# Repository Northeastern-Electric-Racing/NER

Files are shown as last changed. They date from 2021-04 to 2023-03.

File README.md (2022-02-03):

View this project on [CADLAB.io](https://cadlab.io/project/23137/master/files). 

# NER
This is the GitHub repo for all code and schematics created for Northeastern's Electric Racing club.

- Embedded Software: Contains all new embedded code for the Teensy microcontrollers
    - Use Platformio (VS Code plugin) for building and uploading software
        - To install, follow the directions on [this page](https://docs.platformio.org/en/latest//integration/ide/vscode.html)
        - This involves installing VS Code and setting up the Platformio extension
    - CAN libraries (must install in Platformio for each project): 
        - Teensy: [FlexCAN_T4](https://github.com/tonton81/FlexCAN_T4)
        - Arduino: [Seeed Studio CAN BUS Shield](https://github.com/Seeed-Studio/CAN_BUS_Shield)
- ArduinoCode: Old Arduino code for electrical subsystems, NOT UPDATED
    - Required CAN library: [Seeed Studio CAN BUS Shield](https://github.com/Seeed-Studio/CAN_BUS_Shield)
    - To install:
        1. Open the arduino IDE
        2. Go to Tools -> Manage Libraries...
        3. Search "CAN-BUS Shield" and install the associated library
- Schematics: Electrical schematics, created in KiCad, viewable online in CADlab.io or in the desktop client
- Project Manangement: This area has migrated to the [NER-PM-Dashboard repo](https://github.com/Northeastern-Electric-Racing/NER-PM-Dashboard)

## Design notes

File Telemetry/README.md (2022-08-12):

# Telemetry Python Scripts
Currently only the getCSV.py script is working, which converts the files in the logs directory to a csv file with the processed data. To use, run the following command:
- python getCSV.py -name="fileName.csv" -id=00 -data="Data Name" -n=0
- The flags in the command are optional, but do the following:
  - '-name="fileName.csv"' sets the output csv filename (default is output.txt)
  - '-id=00' sets an id to filter the data on, which must be in decimal (default is no filter to show all data)
  - '-data="Data Name"' sets a filter on the data from a specific id by the name in the description column (default is no filter to show all data from an id)
  - '-n=0' sets the format of the timestamp (0 for default string version or 1 for a numeric value)
- To graph a specific data value, filter by the correct -id and -data parameters and use a value of 1 for -n, then graphing the data vs timestamp columns in excel should be straightforward
The `drafts` directory contains unfinished scripts, with development moved to the Telemetry Hub

### Input/Output Directories
The scripts process all of the data in the /log_active directory and send an output to the /outputs directory. 
- Place old logs that we don't want to process but still want to keep in the /log_legacy directory

### TODO
- Add more behavior to graphing scripts
- Add full command line to control behavior through one main

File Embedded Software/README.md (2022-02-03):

# TODO
### All boards
- Add EEPROM support

### Dashboard
- Verify shutdown detect/precharge sequencing

### Pedal Box
- Brake pressure sensor updates

### TCU
- Add SD card logging
- Add accelerometer
- Add GPS
- Add Xbee transfers
- Calculations for vehicle speed
- Timestamp data

### Brake Light
- Add diff temp sensor

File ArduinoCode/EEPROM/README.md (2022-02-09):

# New Telemetry Test/Implementation Code

### Functionalities Achieved:

Writing and Reading to/from EEPROM <br />
Writing to SD Card <br />
Writing Sample Sensor Data to SD Card based on saved EEPROM Parameters <br />

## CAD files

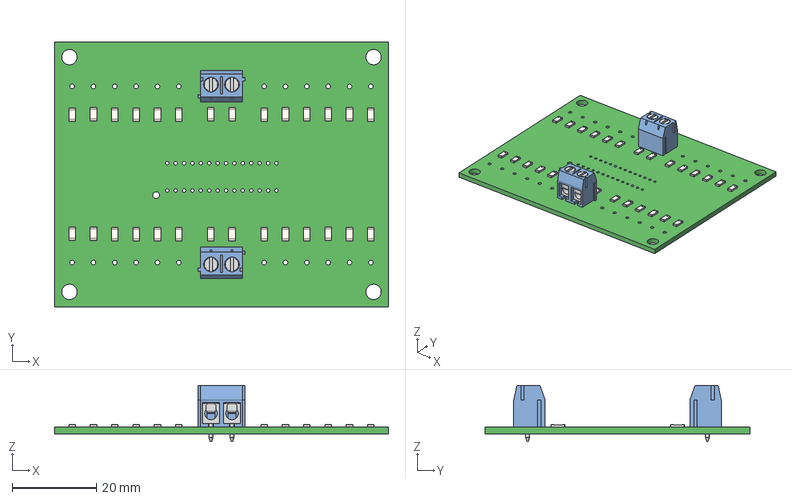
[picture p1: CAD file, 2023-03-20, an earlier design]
Schematics/Shutdown Summary/OLD (Deprecated)/Battery Managment/Therm_PCB/Therms.step
79.5 x 63.0 x 13.4 mm

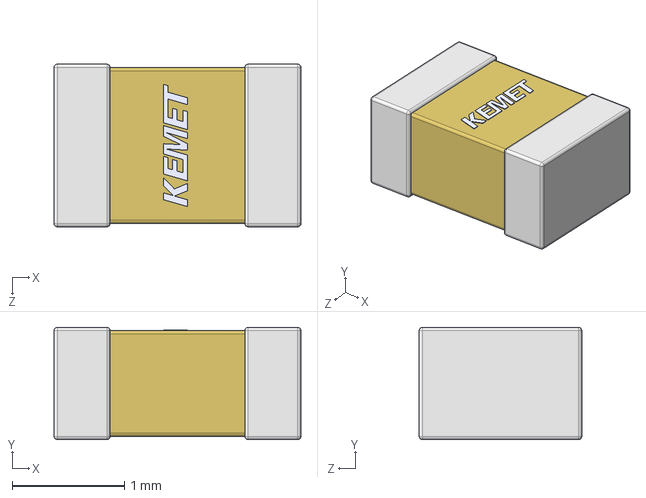
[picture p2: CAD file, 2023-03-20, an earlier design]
Schematics/Shutdown Summary/OLD (Deprecated)/TSAL/TSALpowerboard/3dmodel/C0805C105K9PACTU.STEP
2.20 x 1.00 x 1.45 mm

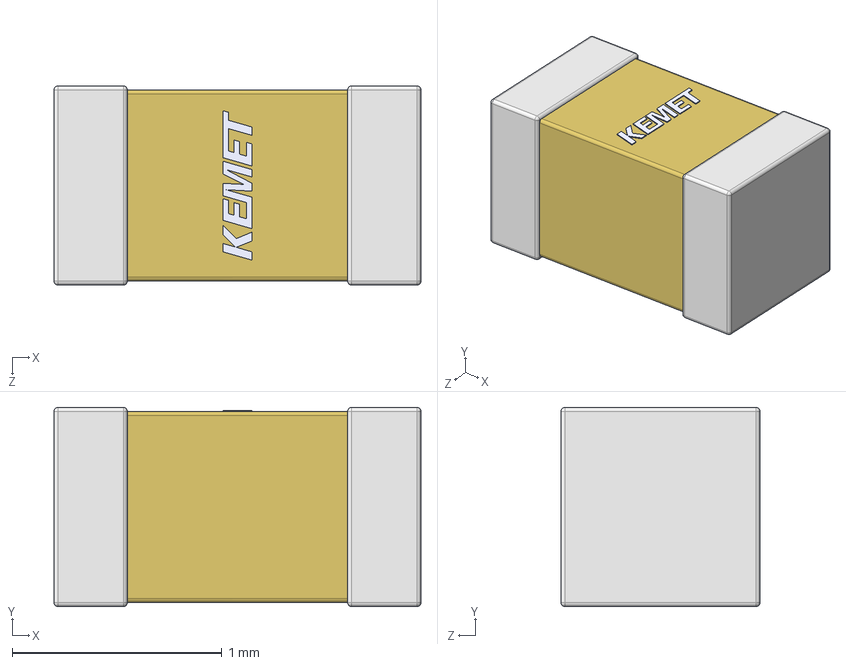
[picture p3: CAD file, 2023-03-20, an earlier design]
Schematics/Shutdown Summary/OLD (Deprecated)/TSAL/Tsalledboard/3dmodel/C0603C105K3RACTU.step
1.75 x 0.95 x 0.95 mm

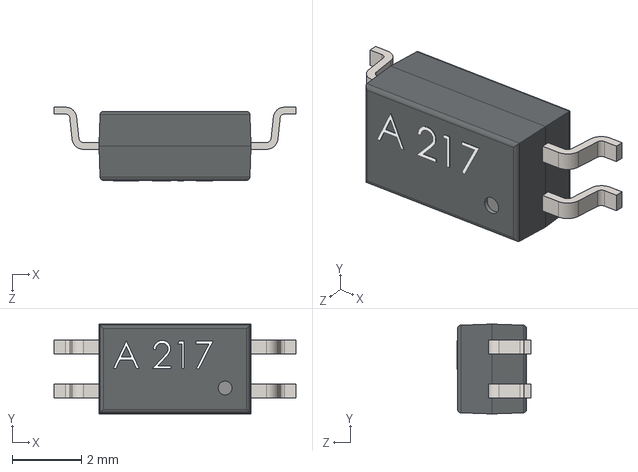
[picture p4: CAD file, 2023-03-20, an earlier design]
Schematics/Shutdown Summary/OLD (Deprecated)/TSAL/TSALpowerboard/3dmodel/User Library-ACPL-217-56DE.STEP
7.00 x 2.60 x 2.13 mm

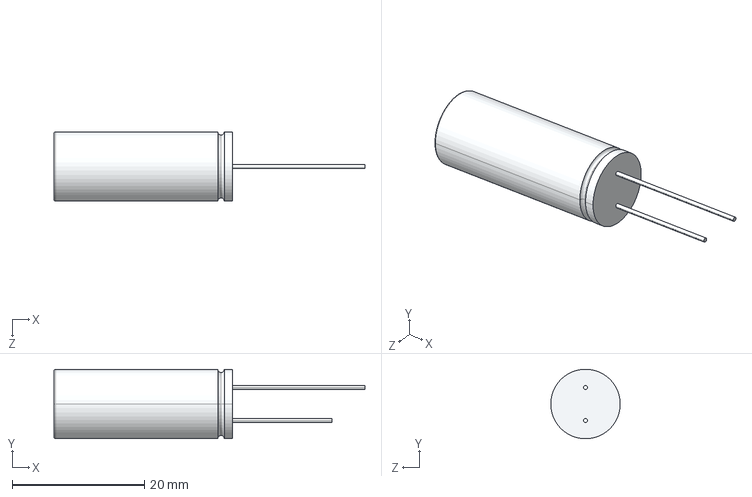
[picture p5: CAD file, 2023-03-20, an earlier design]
Schematics/Shutdown Summary/OLD (Deprecated)/TSAL/Tsalledboard/3dmodel/ESY827M025AH5AA.step
47.0 x 10.5 x 10.5 mm

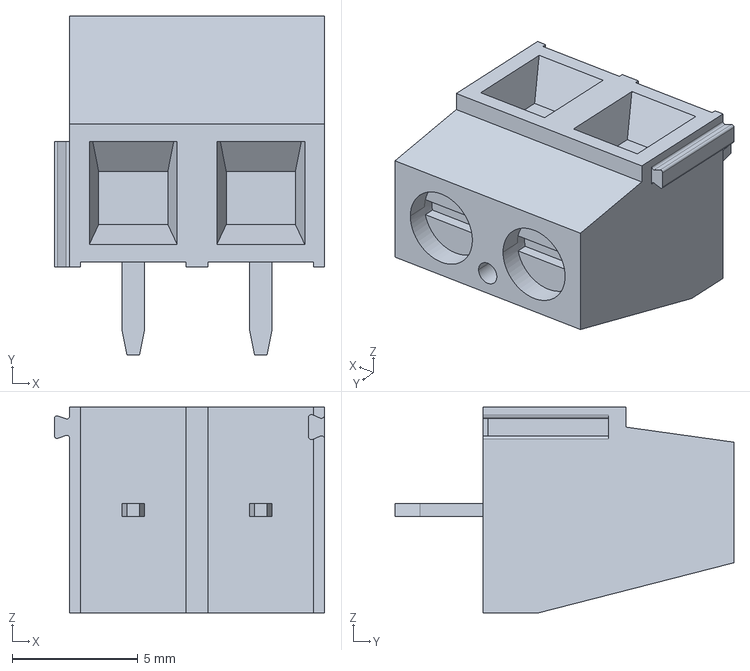
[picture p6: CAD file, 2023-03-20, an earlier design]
Schematics/Shutdown Summary/OLD (Deprecated)/TSAL/TSALpowerboard/3dmodel/c-282837-2-g2-3d.stp
10.8 x 13.5 x 8.20 mm

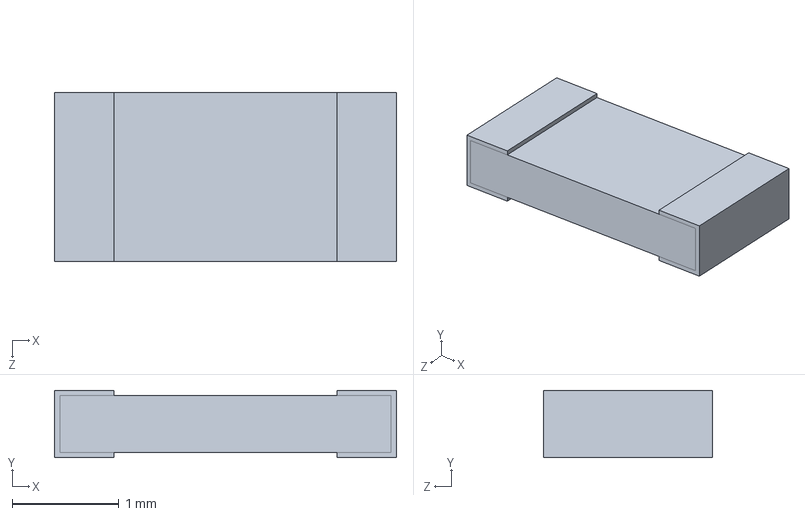
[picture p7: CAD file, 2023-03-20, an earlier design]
Schematics/Shutdown Summary/OLD (Deprecated)/Battery Managment/VoltTap_PCB/C1T5_CAD_Model.SLDPRT
3.20 x 0.63 x 1.58 mm

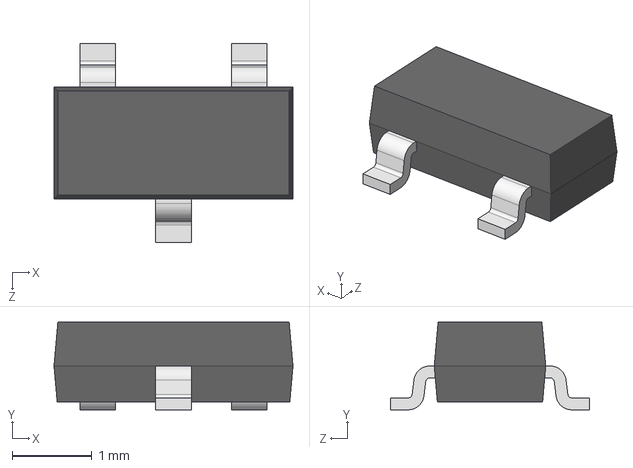
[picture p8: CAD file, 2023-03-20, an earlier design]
Schematics/Shutdown Summary/OLD (Deprecated)/TSAL/Tsalledboard/3dmodel/CircuitWorks-SOT-23.STEP
3.00 x 1.10 x 2.50 mm

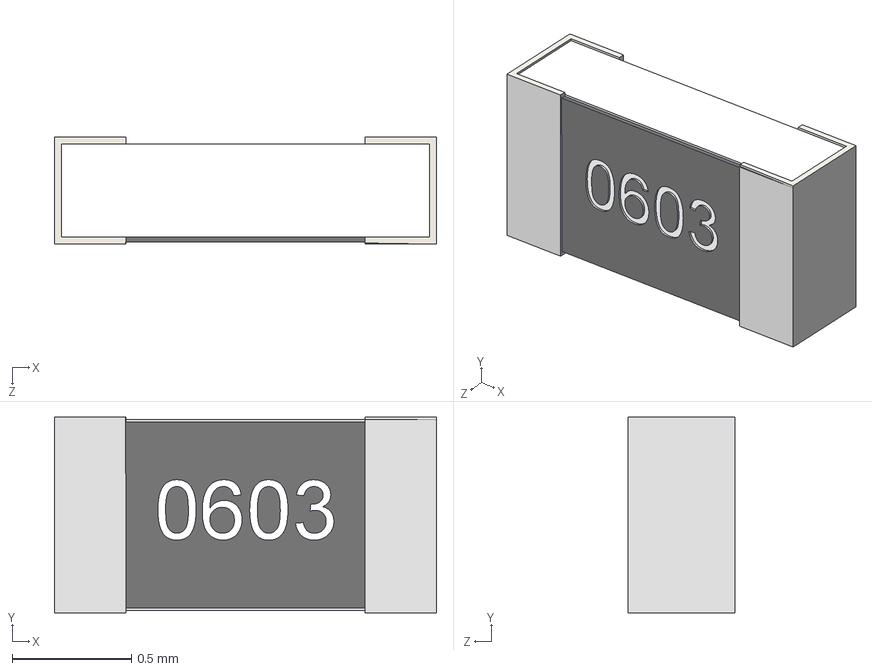
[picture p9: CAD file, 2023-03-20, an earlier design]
Schematics/Shutdown Summary/OLD (Deprecated)/TSAL/TSALpowerboard/3dmodel/Library-Panasonic0603.STEP
1.60 x 0.82 x 0.45 mm

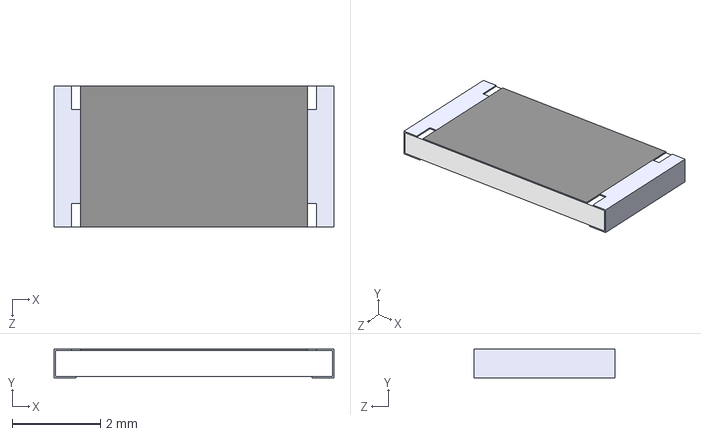
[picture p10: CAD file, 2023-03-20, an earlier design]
Schematics/Shutdown Summary/OLD (Deprecated)/TSAL/Tsalledboard/3dmodel/CRGP2512F560K--3DModel-STEP-46669.STEP
6.35 x 0.65 x 3.20 mm

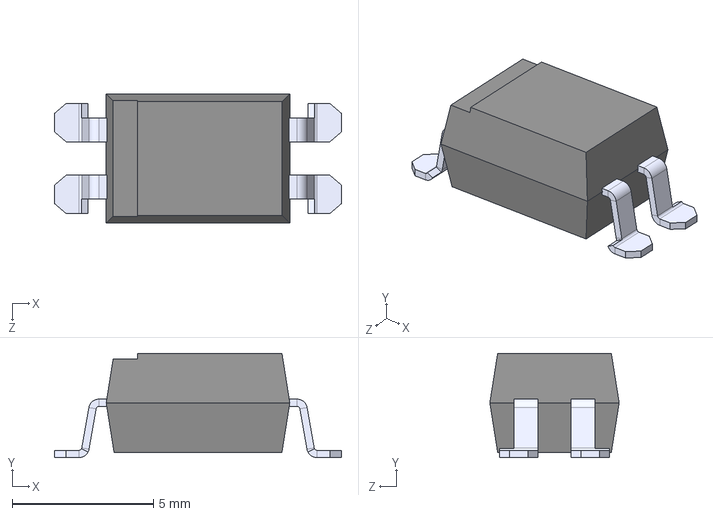
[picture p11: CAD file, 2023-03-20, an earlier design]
Schematics/Shutdown Summary/OLD (Deprecated)/TSAL/TSALpowerboard/3dmodel/SFH617A.STEP
10.2 x 3.69 x 4.58 mm

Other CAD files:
Schematics/Shutdown Summary/OLD (Deprecated)/Battery Managment/VoltTap_PCB/Board.step.SLDASM
Schematics/Shutdown Summary/OLD (Deprecated)/Battery Managment/VoltTap_PCB/C1T5_CAD_Model-0.step.SLDPRT
Schematics/Shutdown Summary/OLD (Deprecated)/Battery Managment/VoltTap_PCB/6120xx22021_LEVIER_COURT.step.SLDPRT
Schematics/Shutdown Summary/OLD (Deprecated)/Battery Managment/VoltTap_PCB/26.step.SLDPRT
Schematics/Shutdown Summary/OLD (Deprecated)/Battery Managment/Therm_PCB/Therms.SLDPRT
Schematics/Shutdown Summary/OLD (Deprecated)/Battery Managment/VoltTap_PCB/6120xx21621_PIN.step.SLDPRT
Schematics/Shutdown Summary/OLD (Deprecated)/Battery Managment/VoltTap_PCB/6911027100xx_CAGE.step.SLDPRT
Schematics/Shutdown Summary/OLD (Deprecated)/Battery Managment/VoltTap_PCB/6911027100xx_PIN.step.SLDPRT
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

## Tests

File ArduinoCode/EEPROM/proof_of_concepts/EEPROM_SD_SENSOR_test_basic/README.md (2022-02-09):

# Second EEPROM Test
### Integrating EEPROM Reading and Writing with SD Card Reading and Writing, Ultrasonic Distance Sensor Sample

Writes sensor parameters to the EEPROM (in this case, 10) to turn on the LED if the distance detected is
less than the specified parameters.
The distance and any important messages are written to the SD card in the DATA.txt file included

## Functionalities:

Writing to SD Card <br />
Reading and Writing to/from EEPROM <br />
Incorporating Sample Sensor (Ultrasonic Distance Sensor) <br />

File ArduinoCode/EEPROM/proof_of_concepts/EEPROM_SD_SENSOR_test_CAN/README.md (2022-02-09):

# Third EEPROM Test
### Using EEPROM Reading and Writing with SD Card Reading and Writing, Ultrasonic Distance Sensor Sample w/ CAN Bus Integration

Has configurable LED output pin and distance sensor parameter based on CAN configuration message. Turns on set LED pin if the ultrasonic distance sensor detects an object within the set parameters.
The distance data and any alerts are written to DATA.txt on an SD card

## TODO

Test Functionality on board <br />

<br />

## Functionalities:

Writing to SD Card <br /> <br />
Reading and Writing to/from EEPROM <br />
Pulling Pin #'s and Parameters from EEPROM <br /> <br />
Reconfiguring Pin #'s and Parameters based on CAN configuration message <br />
Sending configuration message <br /> <br />
Incorporating Sample Sensor (Ultrasonic Distance Sensor) <br />

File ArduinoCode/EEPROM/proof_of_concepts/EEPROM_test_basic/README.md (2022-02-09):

# Initial EEPROM test
###### Writes Data to EEPROM and Reads it

Demonstrates writing to the EEPROM and reading the values by accessing different addresses
Screenshot included is sample reading from the EEPROM

## Functionalities:

Writing and Reading to/from EEPROM

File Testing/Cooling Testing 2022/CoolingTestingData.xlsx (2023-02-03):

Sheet: Fans Only
3.9654 | 4.0475 | 3.7511 | 3.8927 | 3.7594 | 3.9576 | 3.9849 | 3.9842 | 3.9228 | 3.8056 | 4.0448 | 4.0424 | 4.0391 | 4.0897 | 4.0242 | 4.0383 | 4.0366 | 3.7822
Pack Voltage | 71.17
Max Voltage | 4.09
Min Voltage | 3.75
Cell Delta | 0.34
Temperature
25 | 25 | 24 | 25 | 24 | 25 | 25 | 24 | 24 | 24 | 25 | 25 | 25 | 25 | 25 | 25 | 25 | 26 | 25 | 25 | 25 | 25
Voltage
3.9654 | 4.0475 | 3.7511 | 3.8928 | 3.7595 | 3.9575 | 3.9849 | 3.9841 | 3.9228 | 3.8065 | 4.0447 | 4.0424 | 4.0391 | 4.0898 | 4.0245 | 4.0384 | 4.0363 | 3.7833
Pack Voltage | 71.17
Max Voltage | 4.09
Min Voltage | 3.75
Cell Delta | 0.34
Temperature
25 | 25 | 24 | 25 | 24 | 25 | 25 | 24 | 24 | 24 | 25 | 25 | 25 | 25 | 25 | 25 | 25 | 26 | 25 | 25 | 25 | 25
Voltage
3.826 | 3.9046 | 3.6572 | 3.7705 | 3.6667 | 3.8679 | 3.8842 | 3.8924 | 3.7997 | 3.7151 | 3.9267 | 3.9386 | 3.9272 | 3.9833 | 3.9304 | 3.9452 | 3.9395 | 3.6926
Pack Voltage | 69.27
Max Voltage | 3.98
Min Voltage | 3.66
Cell Delta | 0.33
Temperature
25 | 25 | 24 | 25 | 24 | 25 | 25 | 24 | 24 | 24 | 25 | 25 | 25 | 25 | 25 | 25 | 25 | 26 | 25 | 25 | 25 | 25
Voltage
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

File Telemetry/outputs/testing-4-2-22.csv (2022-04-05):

time | message_id | description | value
2021-01-01T00:00:01.633Z | 171 | POST Fault Lo | 0000000000000000
2021-01-01T00:00:01.633Z | 171 | POST Fault Hi | 0000000000000000
2021-01-01T00:00:01.633Z | 171 | Run Fault Lo | 0000100000000000
2021-01-01T00:00:01.633Z | 171 | Run Fault Hi | 0000000000000000
2021-01-01T00:00:03.638Z | 171 | POST Fault Lo | 0000000000000000
2021-01-01T00:00:03.638Z | 171 | POST Fault Hi | 0000000000000000
2021-01-01T00:00:03.638Z | 171 | Run Fault Lo | 0000100000000000
2021-01-01T00:00:03.638Z | 171 | Run Fault Hi | 0000000000000000
2021-01-01T00:00:06.141Z | 171 | POST Fault Lo | 0000000000000000
2021-01-01T00:00:06.141Z | 171 | POST Fault Hi | 0000000000000000
2021-01-01T00:00:06.141Z | 171 | Run Fault Lo | 0000100000000000
2021-01-01T00:00:06.141Z | 171 | Run Fault Hi | 0000000000000000
2021-01-01T00:00:07.690Z | 171 | POST Fault Lo | 0000000000000000
2021-01-01T00:00:07.690Z | 171 | POST Fault Hi | 0000000000000000
2021-01-01T00:00:07.690Z | 171 | Run Fault Lo | 0000100000000000
2021-01-01T00:00:07.690Z | 171 | Run Fault Hi | 0000000000000000
2021-01-01T00:00:09.639Z | 171 | POST Fault Lo | 0000000000000000
2021-01-01T00:00:09.639Z | 171 | POST Fault Hi | 0000000000000000
2021-01-01T00:00:09.639Z | 171 | Run Fault Lo | 0000100000000000
2021-01-01T00:00:09.639Z | 171 | Run Fault Hi | 0000000000000000
2021-01-01T00:00:11.638Z | 171 | POST Fault Lo | 0000000000000000
2021-01-01T00:00:11.638Z | 171 | POST Fault Hi | 0000000000000000
2021-01-01T00:00:11.638Z | 171 | Run Fault Lo | 0000100000000000
2021-01-01T00:00:11.638Z | 171 | Run Fault Hi | 0000000000000000
2021-01-01T00:00:13.790Z | 171 | POST Fault Lo | 0000000000000000
2021-01-01T00:00:13.790Z | 171 | POST Fault Hi | 0000000000000000
2021-01-01T00:00:13.790Z | 171 | Run Fault Lo | 0000100000000000
2021-01-01T00:00:13.790Z | 171 | Run Fault Hi | 0000000000000000
2021-01-01T00:00:15.647Z | 171 | POST Fault Lo | 0000000000000000
2021-01-01T00:00:15.647Z | 171 | POST Fault Hi | 0000000000000000
2021-01-01T00:00:15.647Z | 171 | Run Fault Lo | 0000100000000000
2021-01-01T00:00:15.647Z | 171 | Run Fault Hi | 0000000000000000
2021-01-01T00:00:17.647Z | 171 | POST Fault Lo | 0000000000000000
2021-01-01T00:00:17.647Z | 171 | POST Fault Hi | 0000000000000000
2021-01-01T00:00:17.647Z | 171 | Run Fault Lo | 0000100000000000
2021-01-01T00:00:17.647Z | 171 | Run Fault Hi | 0000000000000000
2021-01-01T00:00:19.897Z | 171 | POST Fault Lo | 0000000000000000
2021-01-01T00:00:19.897Z | 171 | POST Fault Hi | 0000000000000000
2021-01-01T00:00:19.897Z | 171 | Run Fault Lo | 0000100000000000
2021-01-01T00:00:19.897Z | 171 | Run Fault Hi | 0000000000000000
2021-01-01T00:00:21.644Z | 171 | POST Fault Lo | 0000000000000000
2021-01-01T00:00:21.644Z | 171 | POST Fault Hi | 0000000000000000
2021-01-01T00:00:21.644Z | 171 | Run Fault Lo | 0000100000000000
2021-01-01T00:00:21.644Z | 171 | Run Fault Hi | 0000000000000000
2021-01-01T00:00:23.655Z | 171 | POST Fault Lo | 0000000000000000
2021-01-01T00:00:23.655Z | 171 | POST Fault Hi | 0000000000000000
2021-01-01T00:00:23.655Z | 171 | Run Fault Lo | 0000100000000000
2021-01-01T00:00:23.655Z | 171 | Run Fault Hi | 0000000000000000
2021-01-01T00:00:25.971Z | 171 | POST Fault Lo | 0000000000000000
2021-01-01T00:00:25.971Z | 171 | POST Fault Hi | 0000000000000000
2021-01-01T00:00:25.971Z | 171 | Run Fault Lo | 0000100000000000
2021-01-01T00:00:25.971Z | 171 | Run Fault Hi | 0000000000000000
2021-01-01T00:00:27.656Z | 171 | POST Fault Lo | 0000000000000000
2021-01-01T00:00:27.656Z | 171 | POST Fault Hi | 0000000000000000
2021-01-01T00:00:27.656Z | 171 | Run Fault Lo | 0000100000000000
2021-01-01T00:00:27.656Z | 171 | Run Fault Hi | 0000000000000000
2021-01-01T00:00:29.647Z | 171 | POST Fault Lo | 0000000000000000
2021-01-01T00:00:29.647Z | 171 | POST Fault Hi | 0000000000000000
2021-01-01T00:00:29.647Z | 171 | Run Fault Lo | 0000100000000000
2021-01-01T00:00:29.647Z | 171 | Run Fault Hi | 0000000000000000
2021-01-01T00:00:32.027Z | 171 | POST Fault Lo | 0000000000000000
2021-01-01T00:00:32.027Z | 171 | POST Fault Hi | 0000000000000000
2021-01-01T00:00:32.027Z | 171 | Run Fault Lo | 0000100000000000
2021-01-01T00:00:32.027Z | 171 | Run Fault Hi | 0000000000000000
2021-01-01T00:00:33.649Z | 171 | POST Fault Lo | 0000000000000000
2021-01-01T00:00:33.649Z | 171 | POST Fault Hi | 0000000000000000
2021-01-01T00:00:33.649Z | 171 | Run Fault Lo | 0000100000000000
2021-01-01T00:00:33.649Z | 171 | Run Fault Hi | 0000000000000000
2021-01-01T00:00:35.663Z | 171 | POST Fault Lo | 0000000000000000
2021-01-01T00:00:35.663Z | 171 | POST Fault Hi | 0000000000000000
2021-01-01T00:00:35.663Z | 171 | Run Fault Lo | 0000100000000000
2021-01-01T00:00:35.663Z | 171 | Run Fault Hi | 0000000000000000
2021-01-01T00:00:38.072Z | 171 | POST Fault Lo | 0000000000000000
2021-01-01T00:00:38.072Z | 171 | POST Fault Hi | 0000000000000000
2021-01-01T00:00:38.072Z | 171 | Run Fault Lo | 0000100000000000
2021-01-01T00:00:38.072Z | 171 | Run Fault Hi | 0000000000000000
2021-01-01T00:00:39.663Z | 171 | POST Fault Lo | 0000000000000000
2021-01-01T00:00:39.663Z | 171 | POST Fault Hi | 0000000000000000
2021-01-01T00:00:39.663Z | 171 | Run Fault Lo | 0000100000000000
2021-01-01T00:00:39.663Z | 171 | Run Fault Hi | 0000000000000000
2021-01-01T00:00:41.658Z | 171 | POST Fault Lo | 0000000000000000
2021-01-01T00:00:41.658Z | 171 | POST Fault Hi | 0000000000000000
2021-01-01T00:00:41.658Z | 171 | Run Fault Lo | 0000100000000000
2021-01-01T00:00:41.658Z | 171 | Run Fault Hi | 0000000000000000
2021-01-01T00:00:44.119Z | 171 | POST Fault Lo | 0000000000000000
2021-01-01T00:00:44.119Z | 171 | POST Fault Hi | 0000000000000000
2021-01-01T00:00:44.119Z | 171 | Run Fault Lo | 0000100000000000
2021-01-01T00:00:44.119Z | 171 | Run Fault Hi | 0000000000000000
2021-01-01T00:00:45.655Z | 171 | POST Fault Lo | 0000000000000000
2021-01-01T00:00:45.655Z | 171 | POST Fault Hi | 0000000000000000
2021-01-01T00:00:45.655Z | 171 | Run Fault Lo | 0000100000000000
2021-01-01T00:00:45.655Z | 171 | Run Fault Hi | 0000000000000000
2021-01-01T00:00:47.659Z | 171 | POST Fault Lo | 0000000000000000
2021-01-01T00:00:47.659Z | 171 | POST Fault Hi | 0000000000000000
2021-01-01T00:00:47.659Z | 171 | Run Fault Lo | 0000100000000000
2021-01-01T00:00:47.659Z | 171 | Run Fault Hi | 0000000000000000
2021-01-01T00:00:50.147Z | 171 | POST Fault Lo | 0000000000000000
2021-01-01T00:00:50.147Z | 171 | POST Fault Hi | 0000000000000000
2021-01-01T00:00:50.147Z | 171 | Run Fault Lo | 0000100000000000
2021-01-01T00:00:50.147Z | 171 | Run Fault Hi | 0000000000000000
2021-01-01T00:00:51.662Z | 171 | POST Fault Lo | 0000000000000000
2021-01-01T00:00:51.662Z | 171 | POST Fault Hi | 0000000000000000
2021-01-01T00:00:51.662Z | 171 | Run Fault Lo | 0000100000000000
2021-01-01T00:00:51.662Z | 171 | Run Fault Hi | 0000000000000000
2021-01-01T00:00:53.659Z | 171 | POST Fault Lo | 0000000000000000
2021-01-01T00:00:53.659Z | 171 | POST Fault Hi | 0000000000000000
2021-01-01T00:00:53.659Z | 171 | Run Fault Lo | 0000100000000000
2021-01-01T00:00:53.659Z | 171 | Run Fault Hi | 0000000000000000
2021-01-01T00:00:57.671Z | 171 | POST Fault Lo | 0000000000000000
2021-01-01T00:00:57.671Z | 171 | POST Fault Hi | 0000000000000000
2021-01-01T00:00:57.671Z | 171 | Run Fault Lo | 0000100000000000
2021-01-01T00:00:57.671Z | 171 | Run Fault Hi | 0000000000000000
2021-01-01T00:00:59.662Z | 171 | POST Fault Lo | 0000000000000000
2021-01-01T00:00:59.662Z | 171 | POST Fault Hi | 0000000000000000
2021-01-01T00:00:59.662Z | 171 | Run Fault Lo | 0000100000000000
2021-01-01T00:00:59.662Z | 171 | Run Fault Hi | 0000000000000000
2021-01-01T00:01:03.664Z | 171 | POST Fault Lo | 0000000000000000
2021-01-01T00:01:03.664Z | 171 | POST Fault Hi | 0000000000000000
2021-01-01T00:01:03.664Z | 171 | Run Fault Lo | 0000100000000000
2021-01-01T00:01:03.664Z | 171 | Run Fault Hi | 0000000000000000
2021-01-01T00:01:05.671Z | 171 | POST Fault Lo | 0000000000000000
2021-01-01T00:01:05.671Z | 171 | POST Fault Hi | 0000000000000000
2021-01-01T00:01:05.671Z | 171 | Run Fault Lo | 0000100000000000
2021-01-01T00:01:05.671Z | 171 | Run Fault Hi | 0000000000000000
2021-01-01T00:01:07.666Z | 171 | POST Fault Lo | 0000000000000000
2021-01-01T00:01:07.666Z | 171 | POST Fault Hi | 0000000000000000
2021-01-01T00:01:07.666Z | 171 | Run Fault Lo | 0000100000000000
2021-01-01T00:01:07.666Z | 171 | Run Fault Hi | 0000000000000000
2021-01-01T00:01:10.317Z | 171 | POST Fault Lo | 0000000000000000
2021-01-01T00:01:10.317Z | 171 | POST Fault Hi | 0000000000000000
2021-01-01T00:01:10.317Z | 171 | Run Fault Lo | 0000100000000000
2021-01-01T00:01:10.317Z | 171 | Run Fault Hi | 0000000000000000
2021-01-01T00:01:11.668Z | 171 | POST Fault Lo | 0000000000000000
2021-01-01T00:01:11.668Z | 171 | POST Fault Hi | 0000000000000000
2021-01-01T00:01:11.668Z | 171 | Run Fault Lo | 0000100000000000
2021-01-01T00:01:11.668Z | 171 | Run Fault Hi | 0000000000000000
2021-01-01T00:01:13.669Z | 171 | POST Fault Lo | 0000000000000000
2021-01-01T00:01:13.669Z | 171 | POST Fault Hi | 0000000000000000
2021-01-01T00:01:13.669Z | 171 | Run Fault Lo | 0000100000000000
2021-01-01T00:01:13.669Z | 171 | Run Fault Hi | 0000000000000000
2021-01-01T00:01:15.679Z | 171 | POST Fault Lo | 0000000000000000
2021-01-01T00:01:15.679Z | 171 | POST Fault Hi | 0000000000000000
2021-01-01T00:01:15.679Z | 171 | Run Fault Lo | 0000100000000000
2021-01-01T00:01:15.679Z | 171 | Run Fault Hi | 0000000000000000
2021-01-01T00:01:18.221Z | 171 | POST Fault Lo | 0000000000000000
2021-01-01T00:01:18.221Z | 171 | POST Fault Hi | 0000000000000000
2021-01-01T00:01:18.221Z | 171 | Run Fault Lo | 0000100000000000
2021-01-01T00:01:18.221Z | 171 | Run Fault Hi | 0000000000000000
2021-01-01T00:01:19.681Z | 171 | POST Fault Lo | 0000000000000000
2021-01-01T00:01:19.681Z | 171 | POST Fault Hi | 0000000000000000
2021-01-01T00:01:19.681Z | 171 | Run Fault Lo | 0000100000000000
2021-01-01T00:01:19.681Z | 171 | Run Fault Hi | 0000000000000000
2021-01-01T00:01:21.681Z | 171 | POST Fault Lo | 0000000000000000
2021-01-01T00:01:21.681Z | 171 | POST Fault Hi | 0000000000000000
2021-01-01T00:01:21.681Z | 171 | Run Fault Lo | 0000100000000000
2021-01-01T00:01:21.681Z | 171 | Run Fault Hi | 0000000000000000
2021-01-01T00:01:23.673Z | 171 | POST Fault Lo | 0000000000000000
2021-01-01T00:01:23.673Z | 171 | POST Fault Hi | 0000000000000000
2021-01-01T00:01:23.673Z | 171 | Run Fault Lo | 0000100000000000
2021-01-01T00:01:23.673Z | 171 | Run Fault Hi | 0000000000000000
2021-01-01T00:01:25.912Z | 171 | POST Fault Lo | 0000000000000000
2021-01-01T00:01:25.912Z | 171 | POST Fault Hi | 0000000000000000
2021-01-01T00:01:25.912Z | 171 | Run Fault Lo | 0000100000000000
2021-01-01T00:01:25.912Z | 171 | Run Fault Hi | 0000000000000000
2021-01-01T00:01:27.681Z | 171 | POST Fault Lo | 0000000000000000
2021-01-01T00:01:27.681Z | 171 | POST Fault Hi | 0000000000000000
2021-01-01T00:01:27.681Z | 171 | Run Fault Lo | 0000100000000000
2021-01-01T00:01:27.681Z | 171 | Run Fault Hi | 0000000000000000
2021-01-01T00:01:29.682Z | 171 | POST Fault Lo | 0000000000000000
2021-01-01T00:01:29.682Z | 171 | POST Fault Hi | 0000000000000000
2021-01-01T00:01:29.682Z | 171 | Run Fault Lo | 0000100000000000
2021-01-01T00:01:29.682Z | 171 | Run Fault Hi | 0000000000000000
2021-01-01T00:01:33.686Z | 171 | POST Fault Lo | 0000000000000000
2021-01-01T00:01:33.686Z | 171 | POST Fault Hi | 0000000000000000
2021-01-01T00:01:33.686Z | 171 | Run Fault Lo | 0000100000000000
2021-01-01T00:01:33.686Z | 171 | Run Fault Hi | 0000000000000000
2021-01-01T00:01:35.687Z | 171 | POST Fault Lo | 0000000000000000
2021-01-01T00:01:35.687Z | 171 | POST Fault Hi | 0000000000000000
2021-01-01T00:01:35.687Z | 171 | Run Fault Lo | 0000100000000000
2021-01-01T00:01:35.687Z | 171 | Run Fault Hi | 0000000000000000
2021-01-01T00:01:39.743Z | 171 | POST Fault Lo | 0000000000000000
2021-01-01T00:01:39.743Z | 171 | POST Fault Hi | 0000000000000000
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

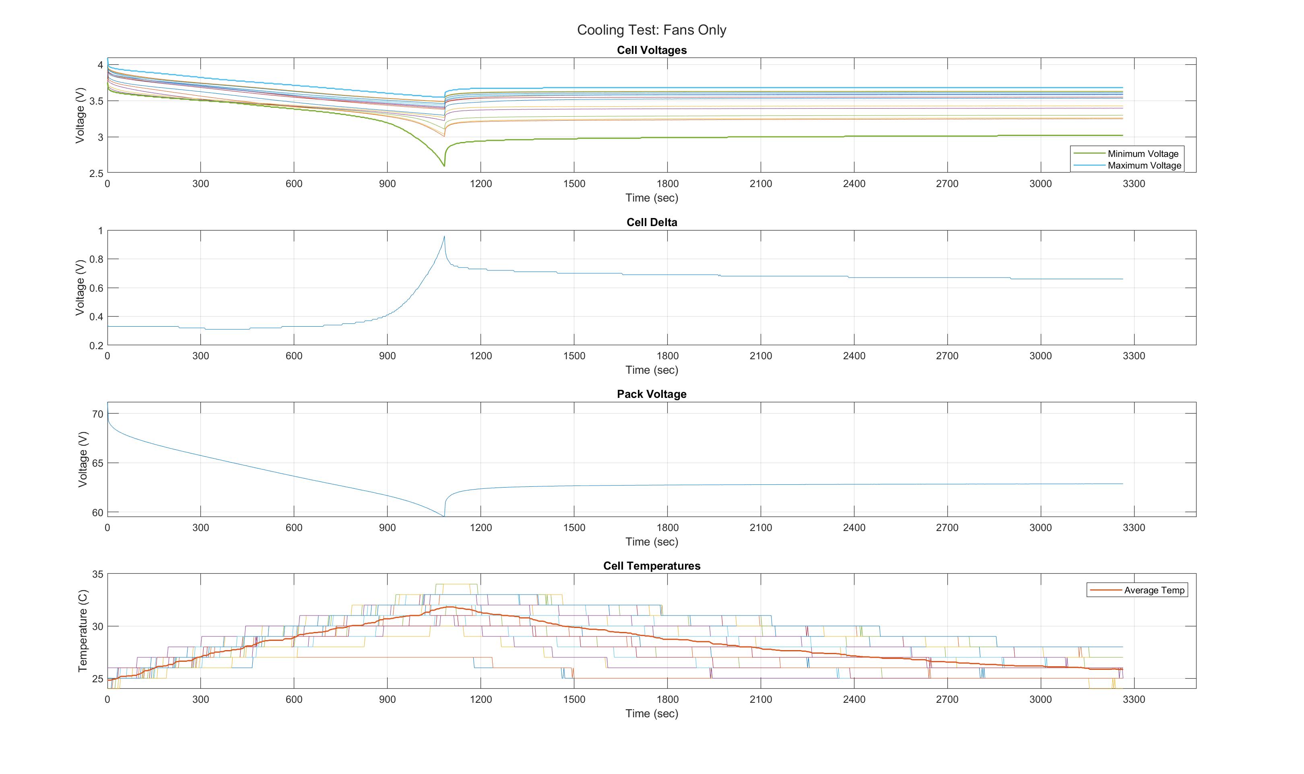
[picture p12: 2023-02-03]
Testing/Cooling Testing 2022/Fans Only.jpg

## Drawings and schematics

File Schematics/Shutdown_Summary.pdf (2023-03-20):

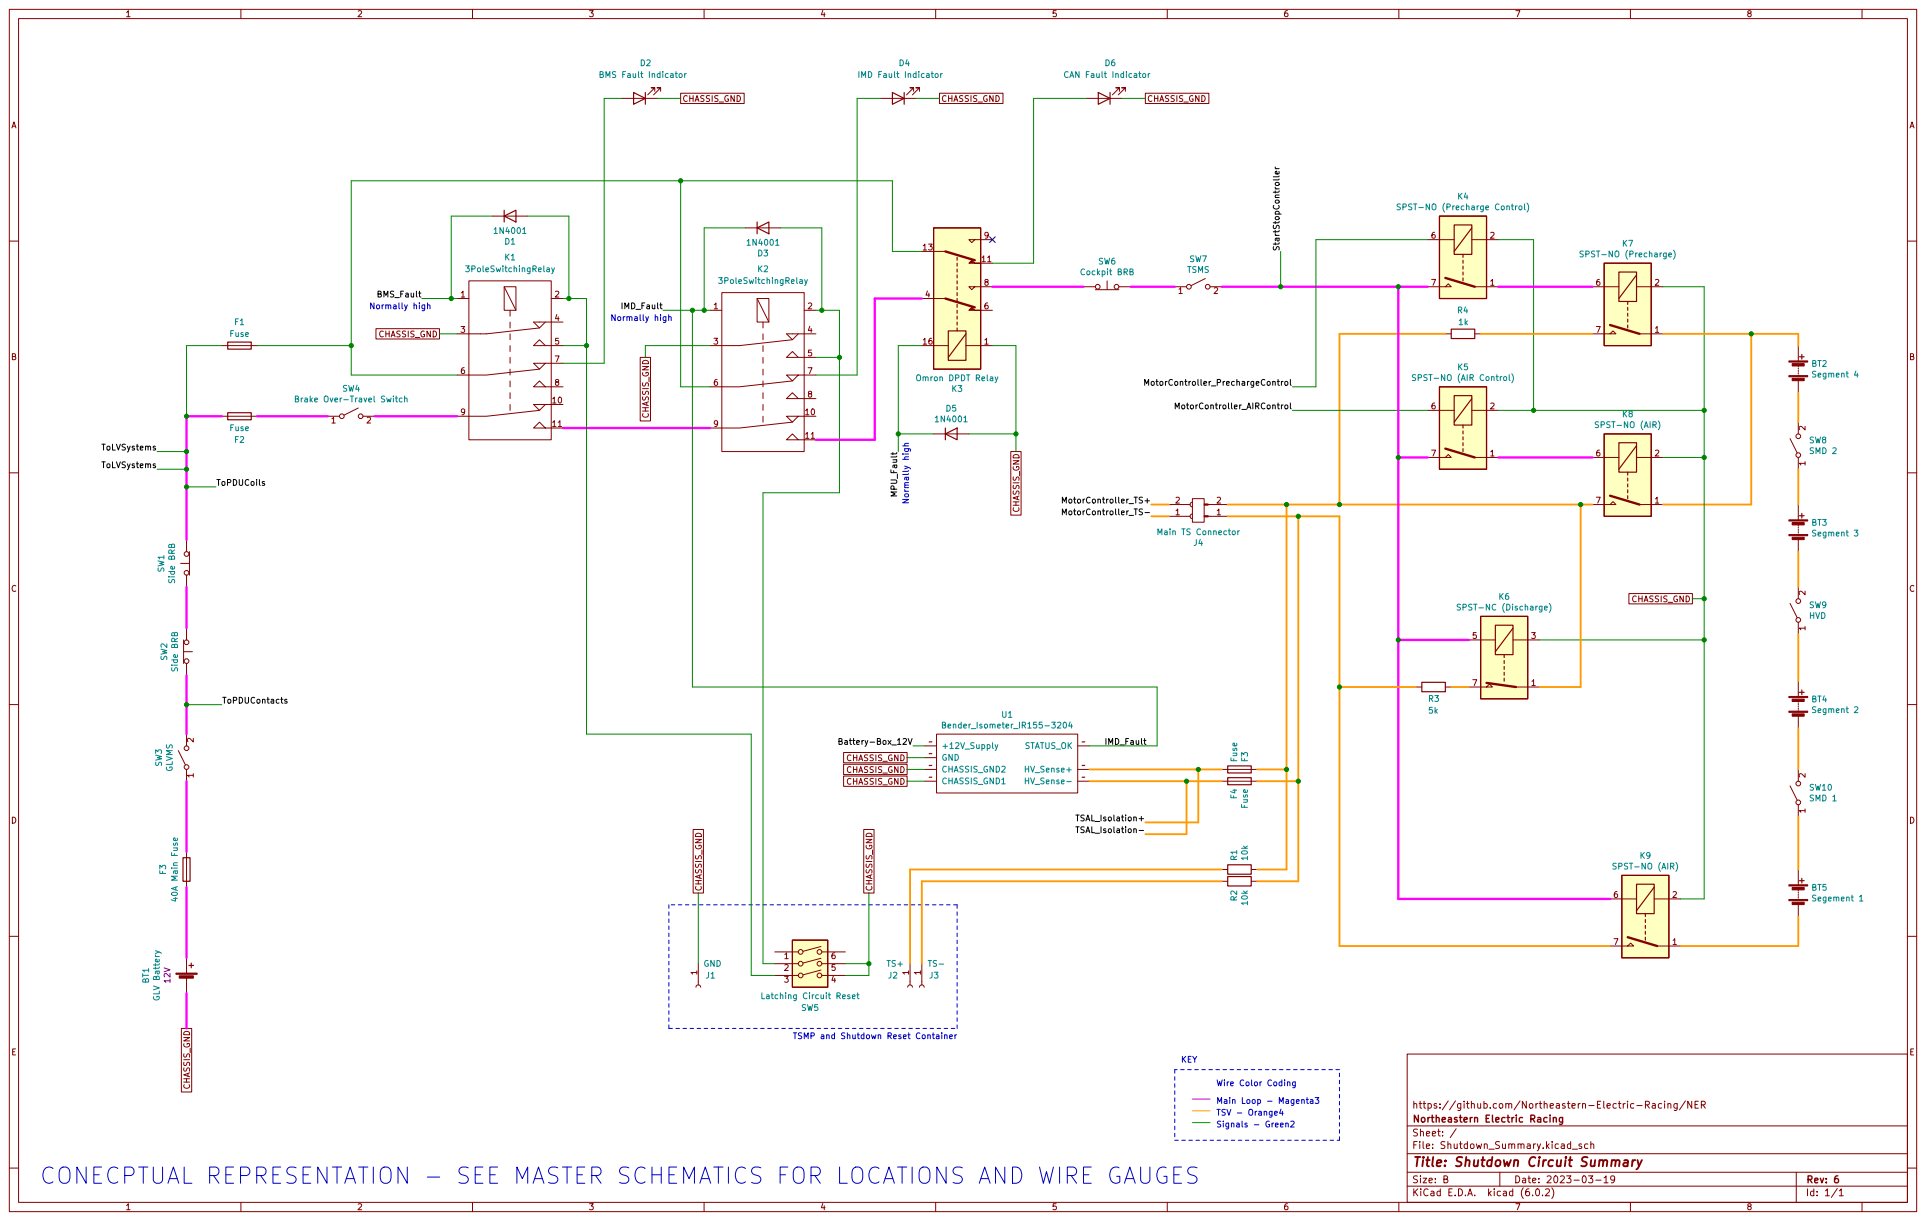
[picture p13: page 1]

1 2 SW8 SMD 2 D6 CAN Fault Indicator D3

Main Loop - Magenta3 KEY Normally high

TSMP and Shutdown Reset Container

https://github.com/Northeastern-Electric-Racing/NER
File: Shutdown_Summary.kicad_sch Sheet: / Northeastern Electric Racing

Id: 1/1 Title: Shutdown Circuit Summary

CONECPTUAL REPRESENTATION - SEE MASTER SCHEMATICS FOR LOCATIONS AND WIRE GAUGES

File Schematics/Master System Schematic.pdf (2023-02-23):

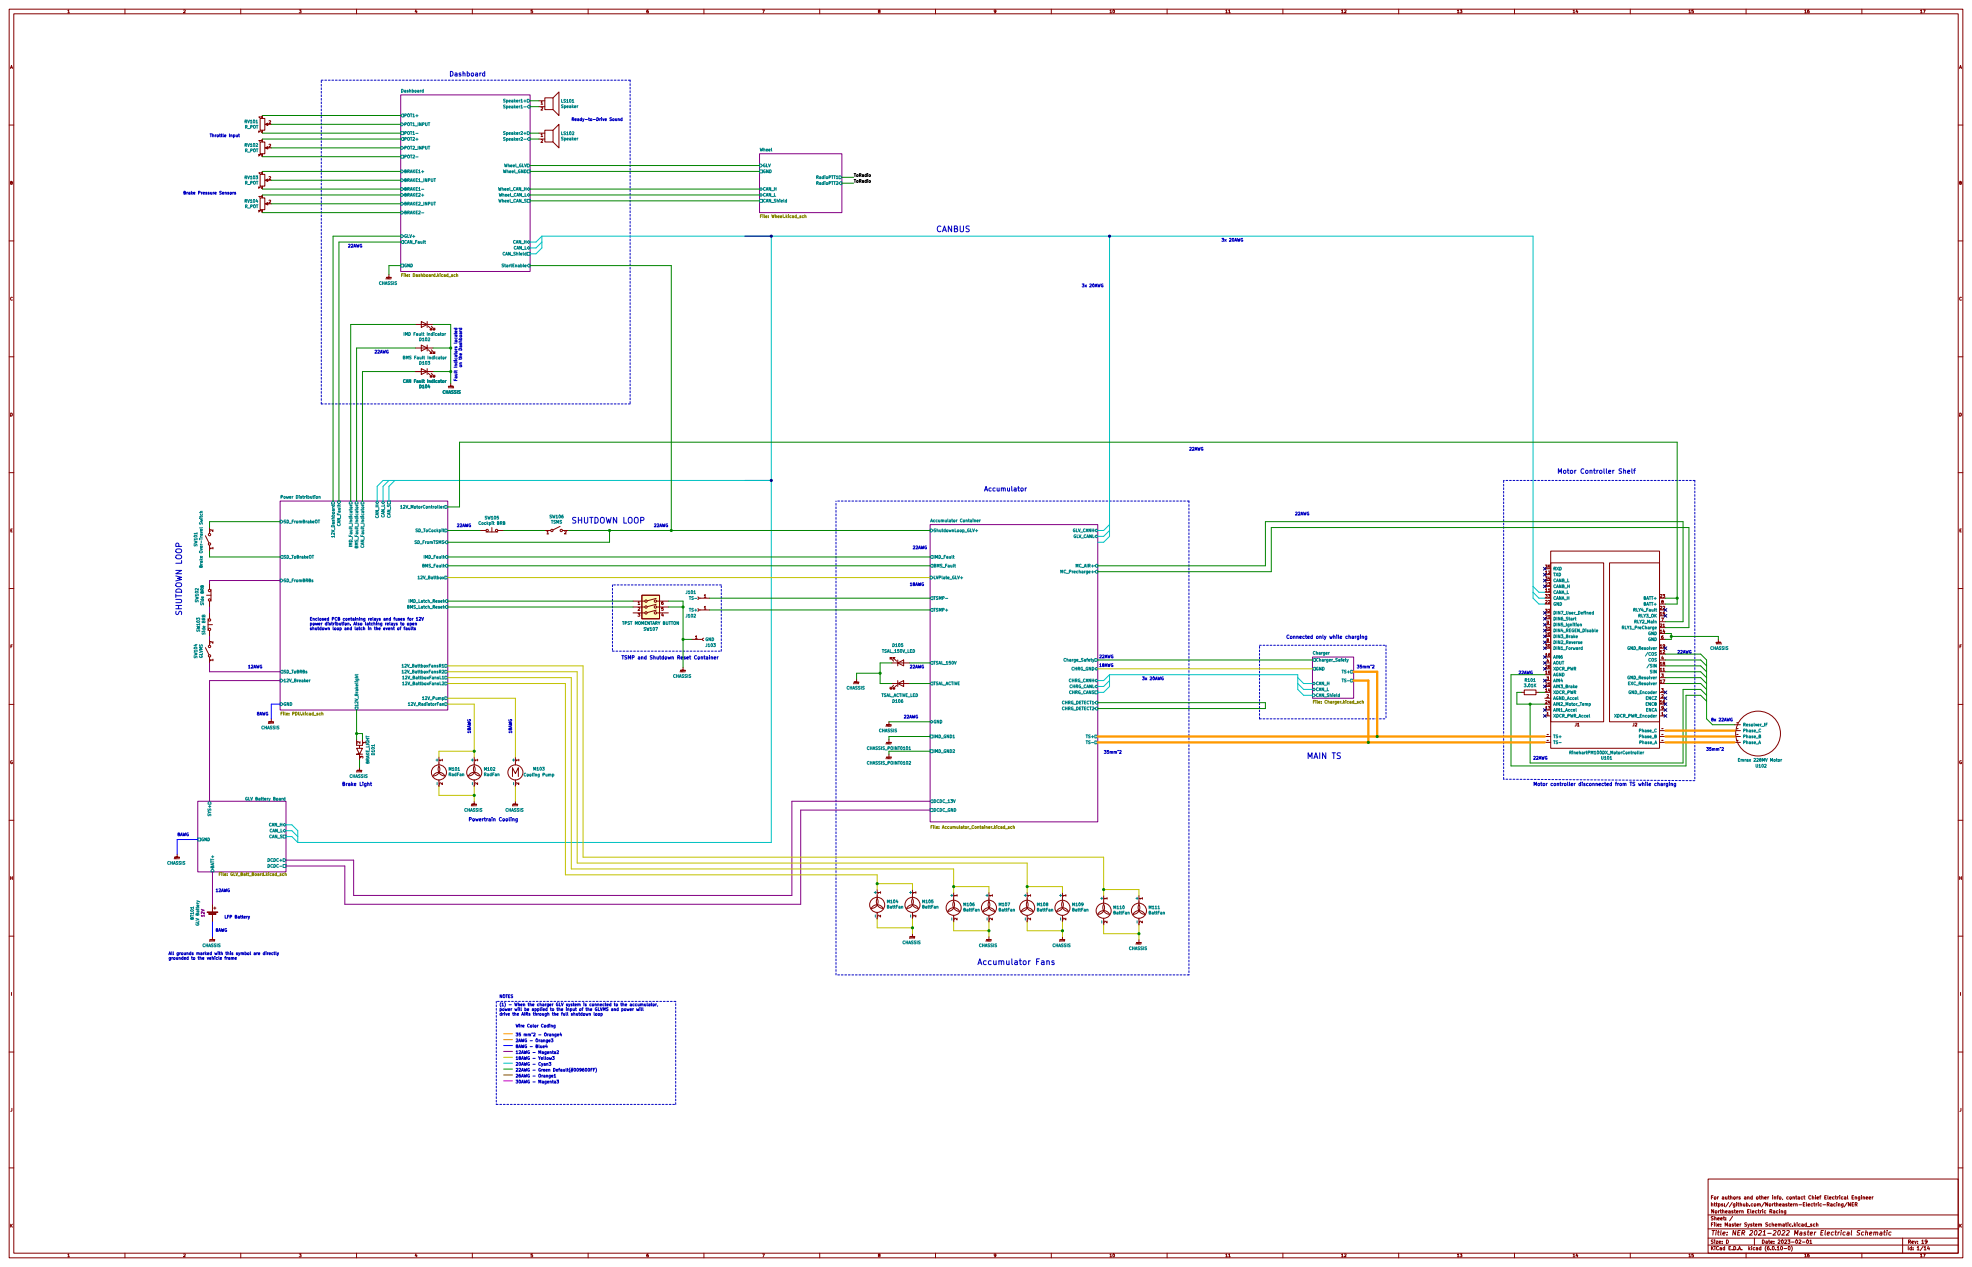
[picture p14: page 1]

LS102 Speaker SW103 Side BRB BT101 GLV Battery 12V

Ready-to-Drive Sound

CHASSIS D104 CAN Fault Indicator
12V_BattboxFansR2 CAN_H CAN_L CAN_S

Power Distribution File: PDU.kicad_sch

1 2 SW101 Brake Over-Travel Switch CHASSIS CHASSIS

Enclosed PCB containing relays and fuses for 12V
power distribution. Also latching relays to open
shutdown loop and latch in the event of faults

TSMP and Shutdown Reset Container

-2 M103 CHASSIS Cooling Pump CHASSIS

CAN_S CAN_L GLV Battery Board File: GLV_Batt_Board.kicad_sch

All grounds marked with this symbol are directly
grounded to the vehicle frame

(1) - When the charger GLV system is connected to the accumulator,
power will be applied to the input of the GLVMS and power will
drive the AIRs through the full shutdown loop

For authors and other info, contact Chief Electrical Engineer
https://github.com/Northeastern-Electric-Racing/NER
File: Master System Schematic.kicad_sch Sheet: / Northeastern Electric Racing

Id: 1/14 Title: NER 2021-2022 Master Electrical Schematic

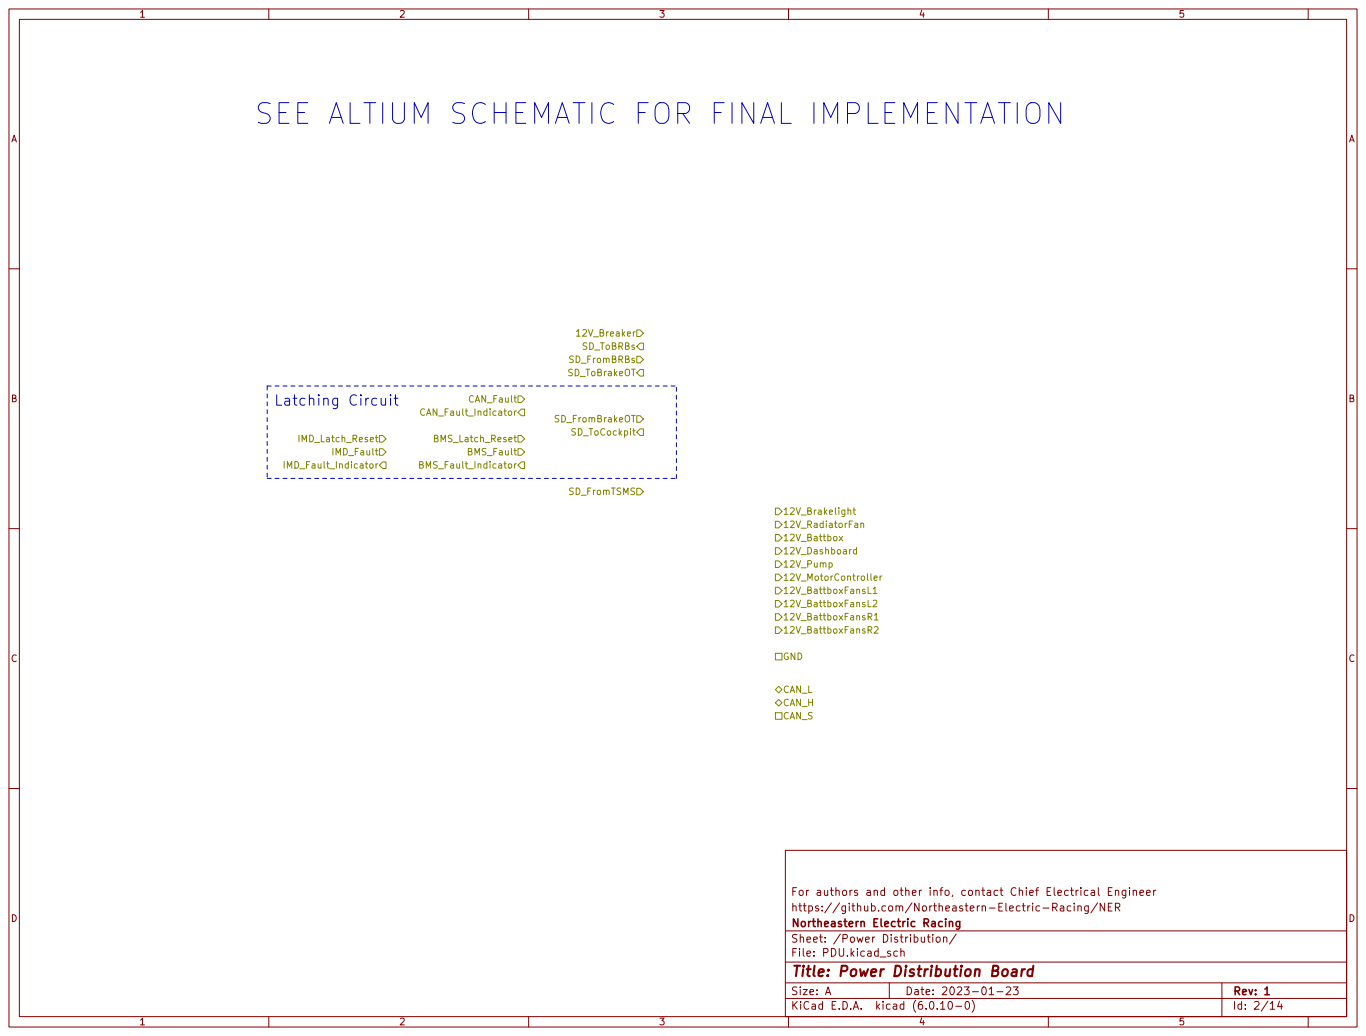
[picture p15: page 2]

SD_FromBrakeOT SEE ALTIUM SCHEMATIC FOR FINAL IMPLEMENTATION

For authors and other info, contact Chief Electrical Engineer
https://github.com/Northeastern-Electric-Racing/NER
File: PDU.kicad_sch Sheet: /Power Distribution/ Northeastern Electric Racing

Id: 2/14 Title: Power Distribution Board

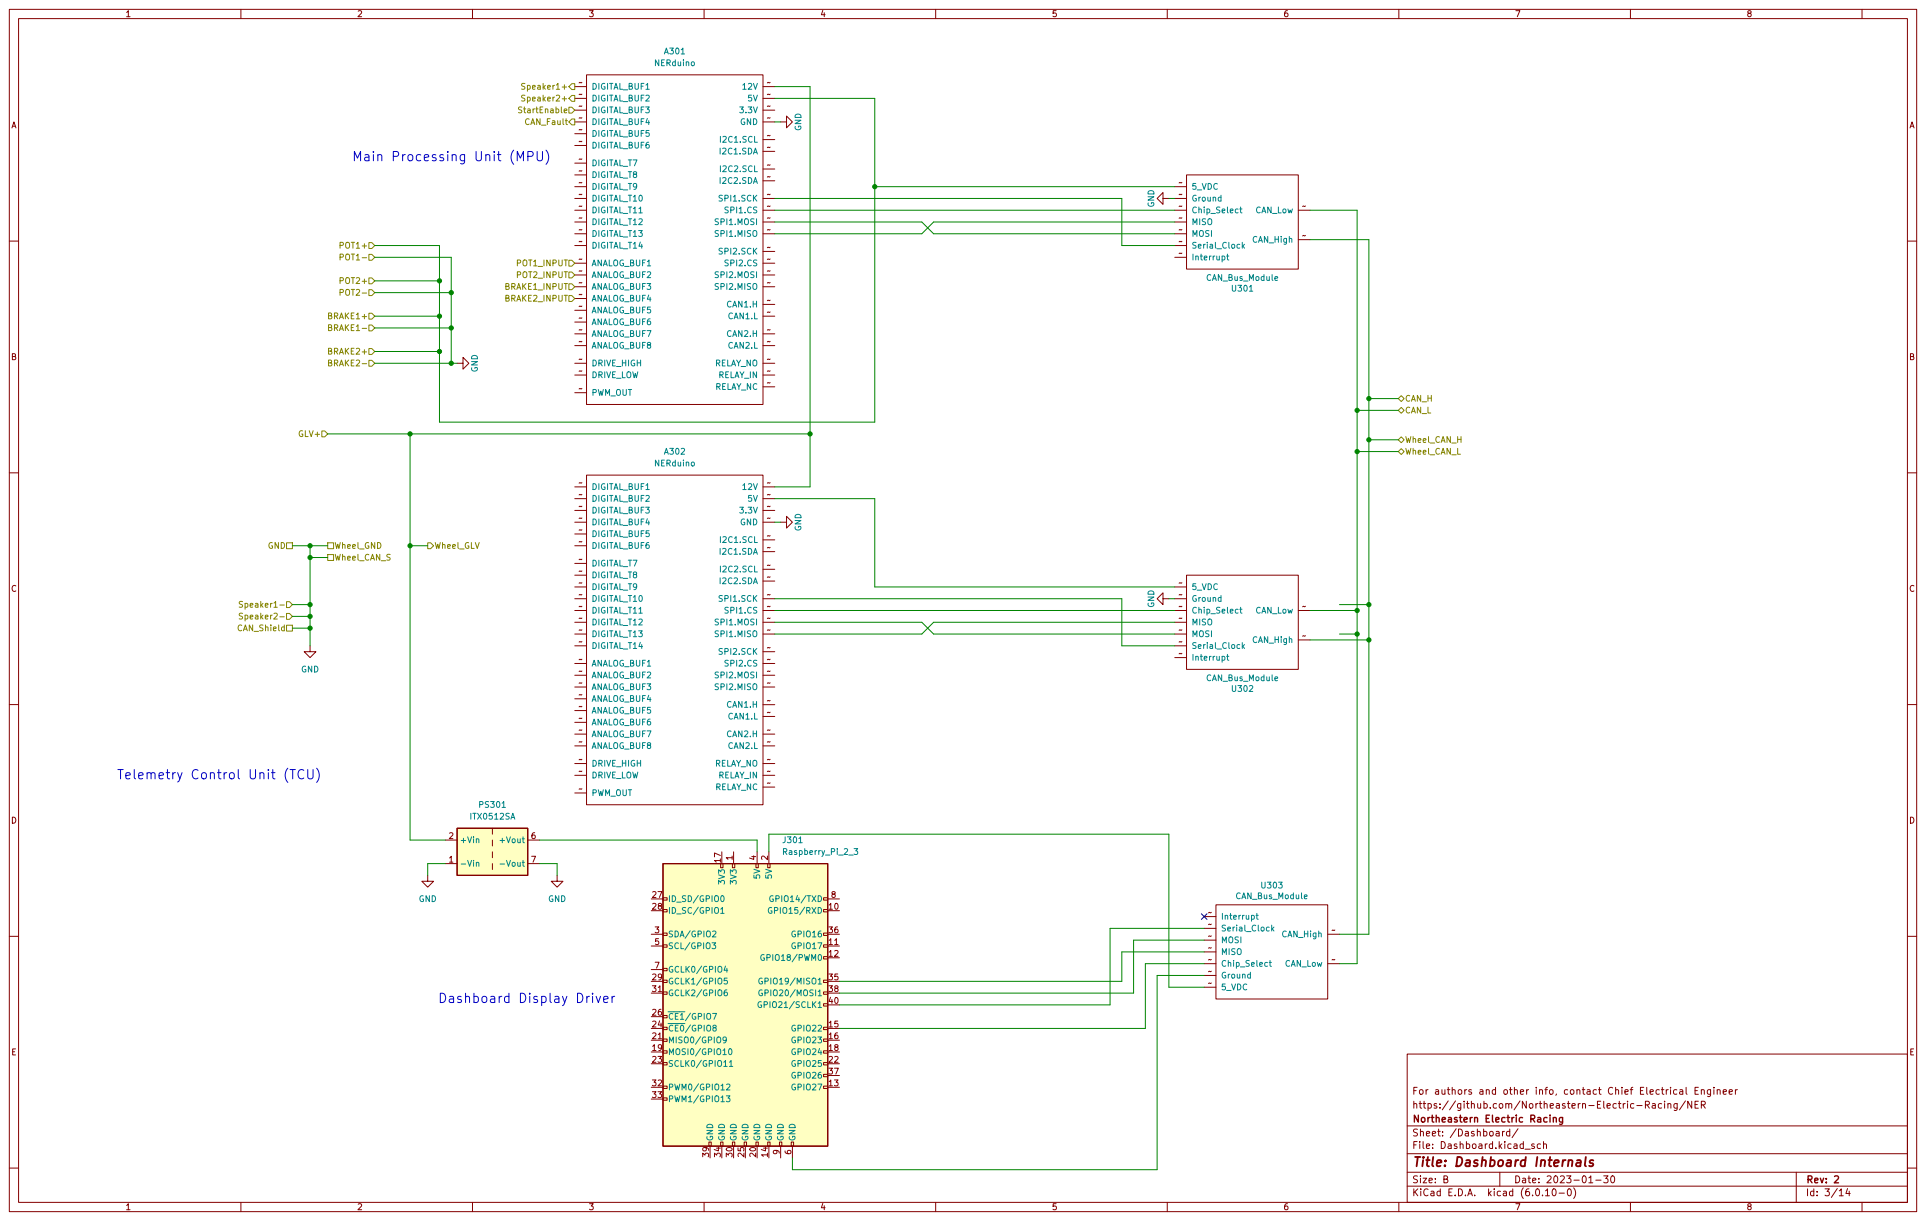
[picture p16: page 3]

Telemetry Control Unit (TCU)

https://github.com/Northeastern-Electric-Racing/NER
File: Dashboard.kicad_sch Sheet: /Dashboard/ Northeastern Electric Racing

Id: 3/14 Title: Dashboard Internals

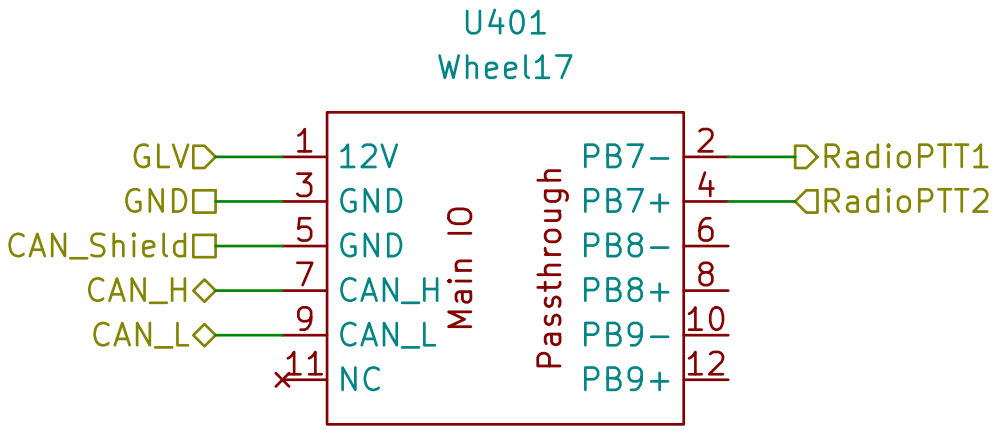
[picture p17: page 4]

https://github.com/Northeastern-Electric-Racing/NER
File: Wheel.kicad_sch Sheet: /Wheel/ Northeastern Electric Racing

Id: 4/14 Title: Wheel PCB

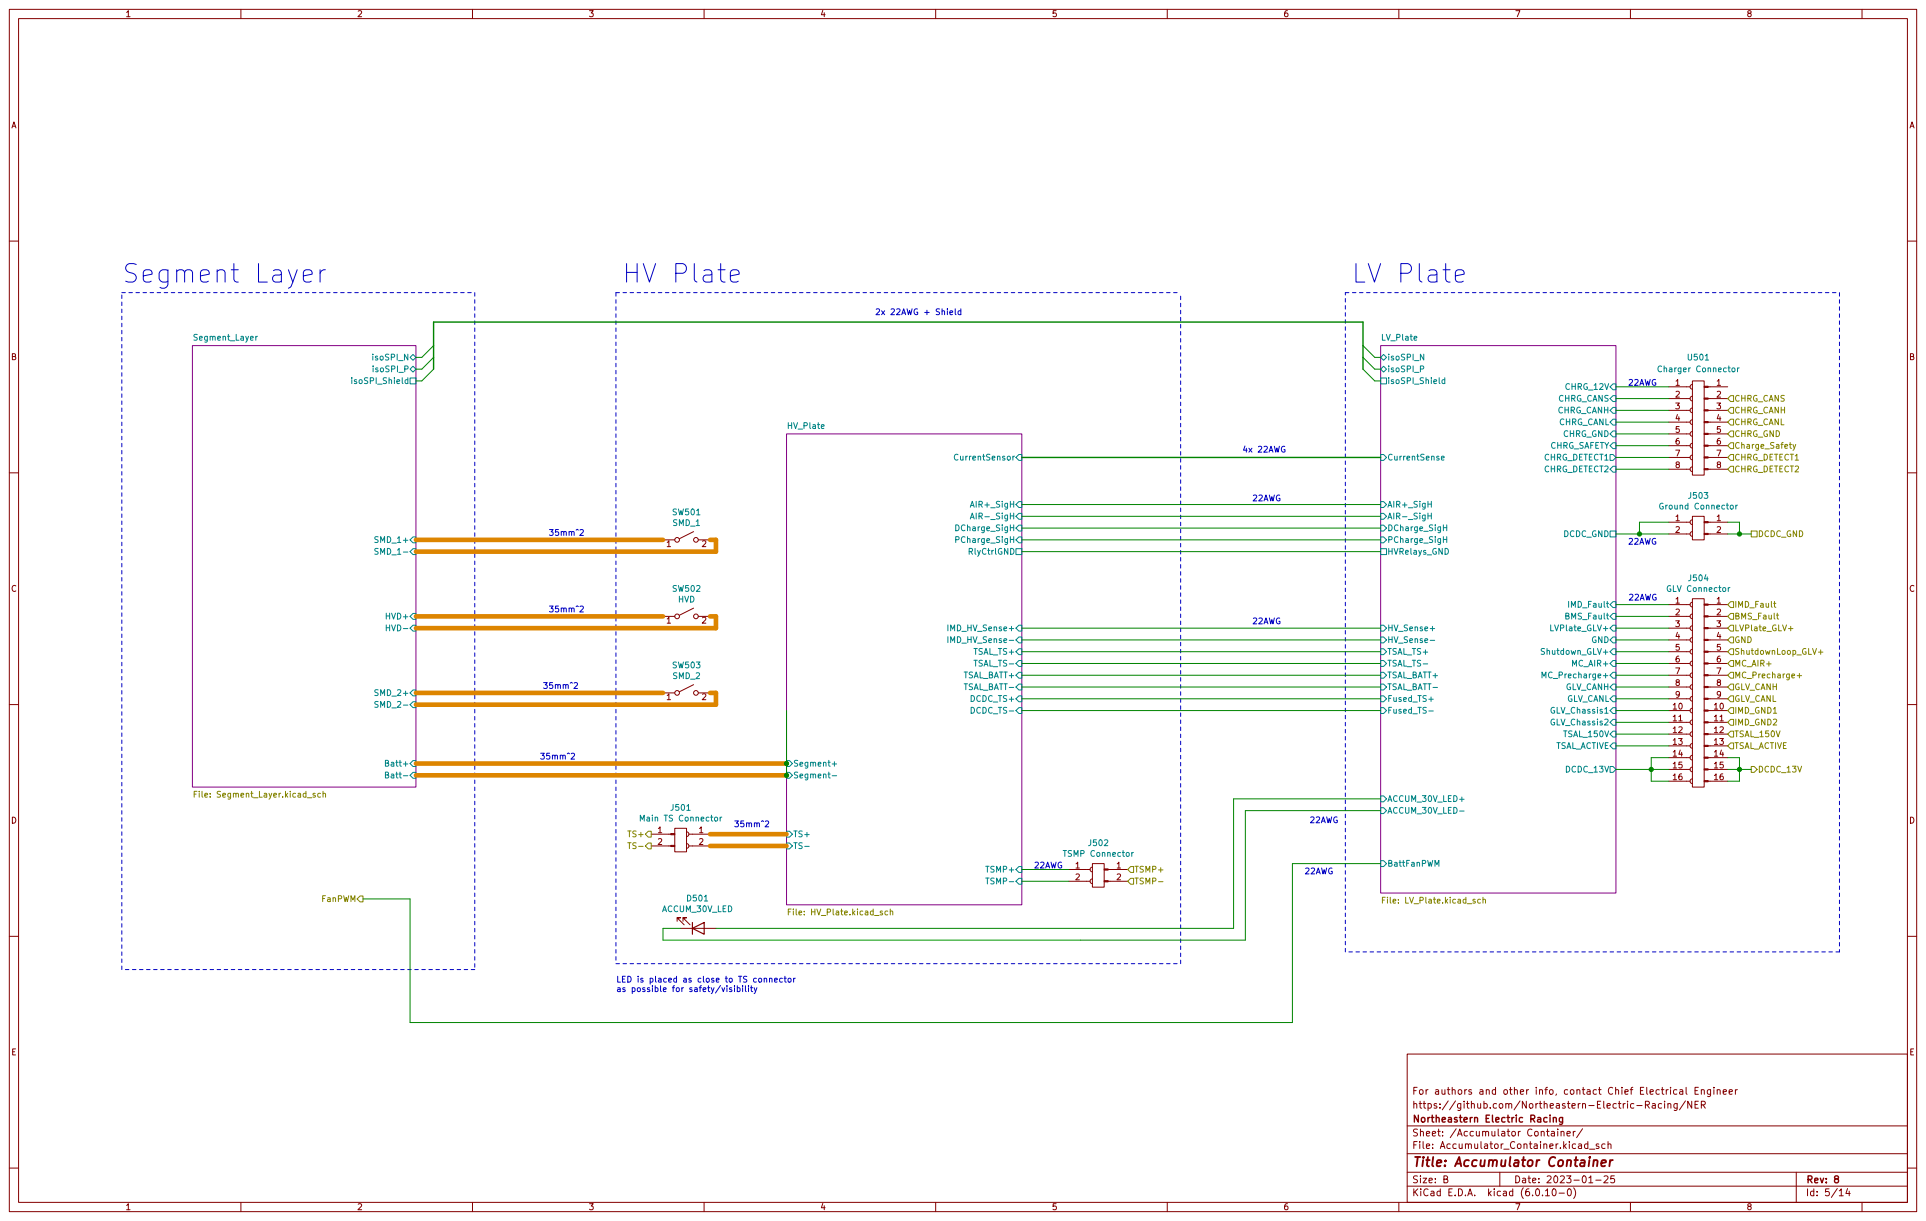
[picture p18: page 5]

DCDC_TS- DCDC_TS+ HV_Plate File: HV_Plate.kicad_sch Batt+ Batt- SMD_2- SMD_2+ HVD- HVD+ SMD_1- SMD_1+ | 22AWG

4x 22AWG

22AWG

35mm^2 | 1 2 SW503 SMD_2

LED is placed as close to TS connector
as possible for safety/visibility

For authors and other info, contact Chief Electrical Engineer
https://github.com/Northeastern-Electric-Racing/NER
File: Accumulator_Container.kicad_sch Sheet: /Accumulator Container/ Northeastern Electric Racing

Id: 5/14 Title: Accumulator Container

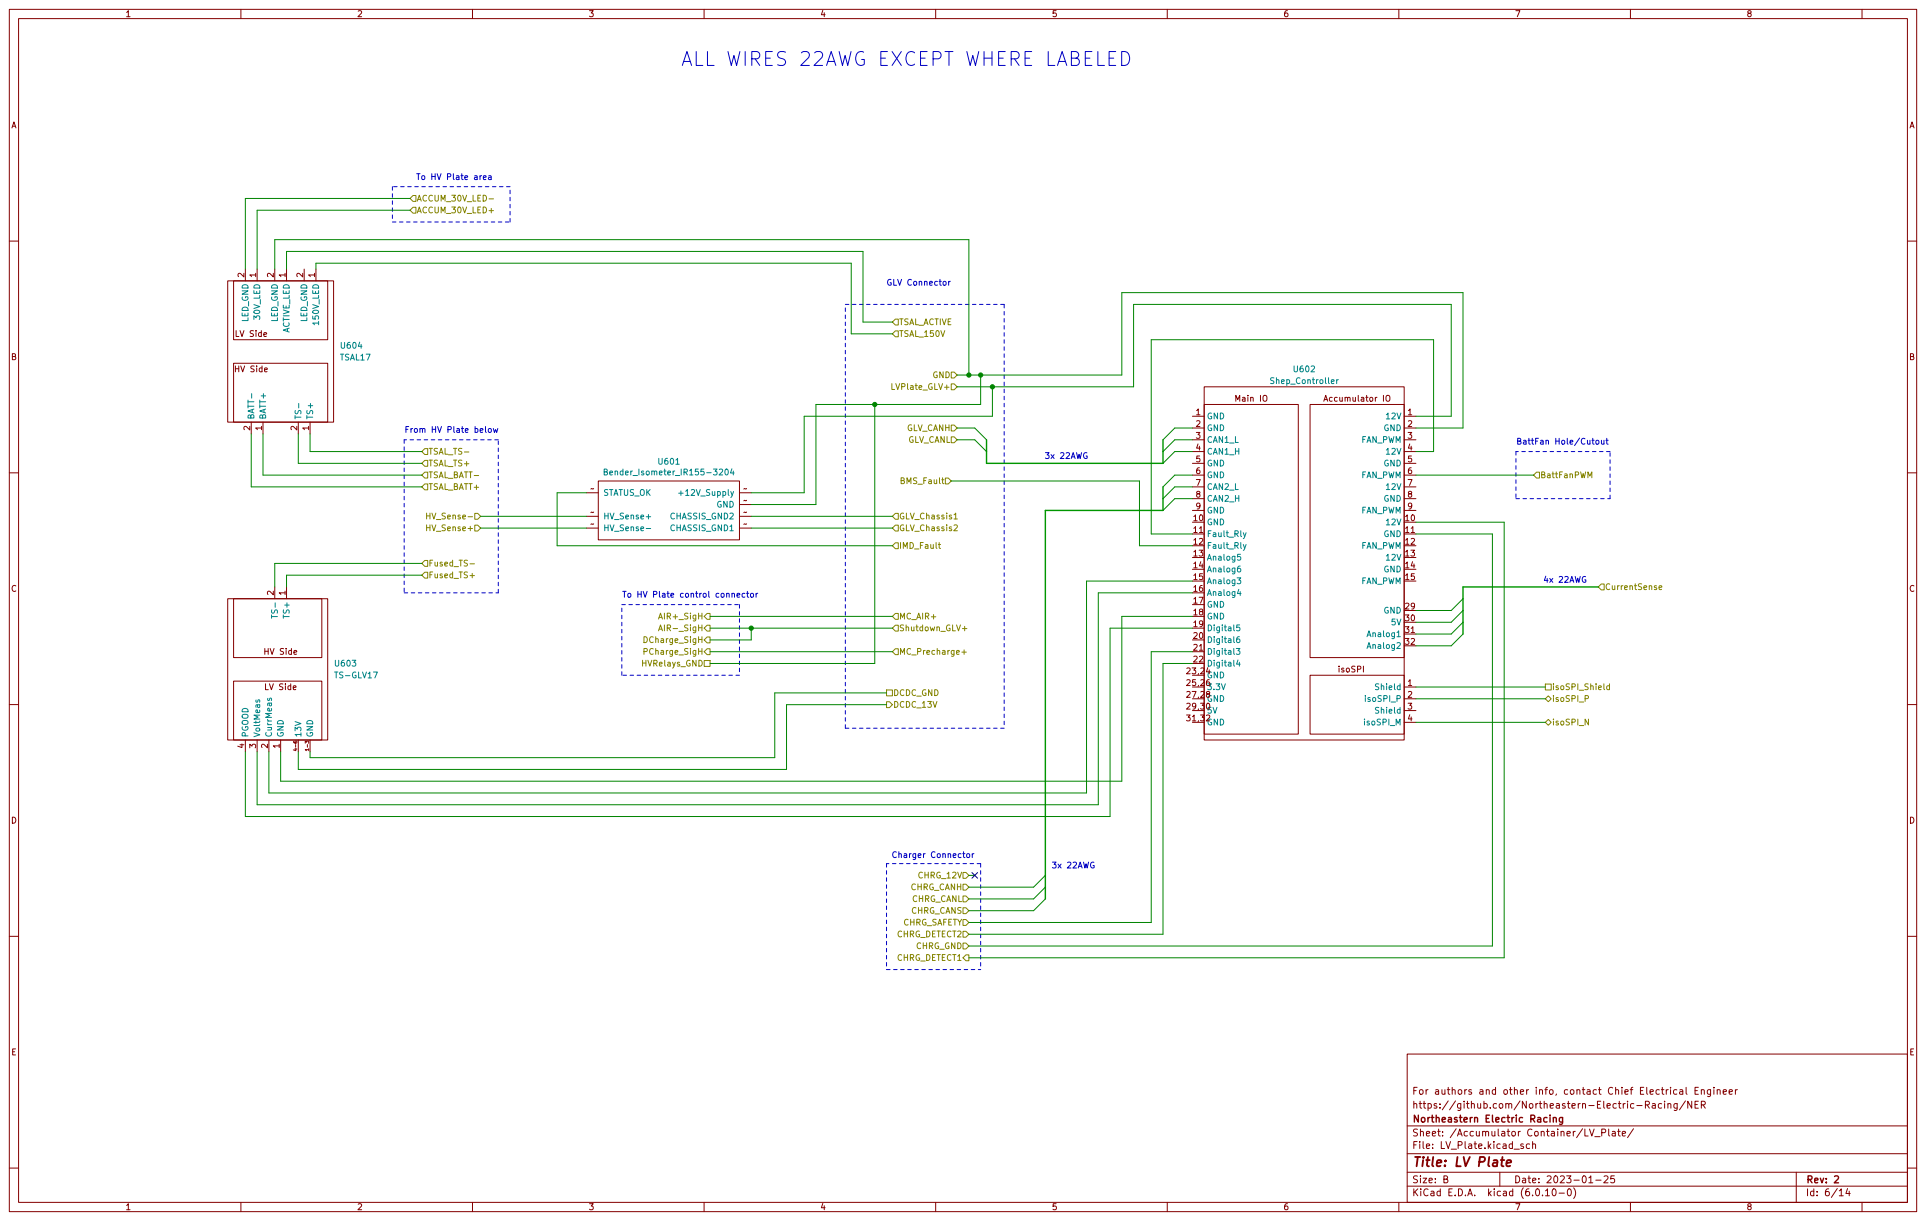
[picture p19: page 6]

ALL WIRES 22AWG EXCEPT WHERE LABELED

To HV Plate area

1 GND 1-3 CurrMeas 2 TS- 2 VoltMeas 3 PGOOD

For authors and other info, contact Chief Electrical Engineer
https://github.com/Northeastern-Electric-Racing/NER
Northeastern Electric Racing
Sheet: /Accumulator Container/LV_Plate/
File: LV_Plate.kicad_sch
Id: 6/14 Title: LV Plate

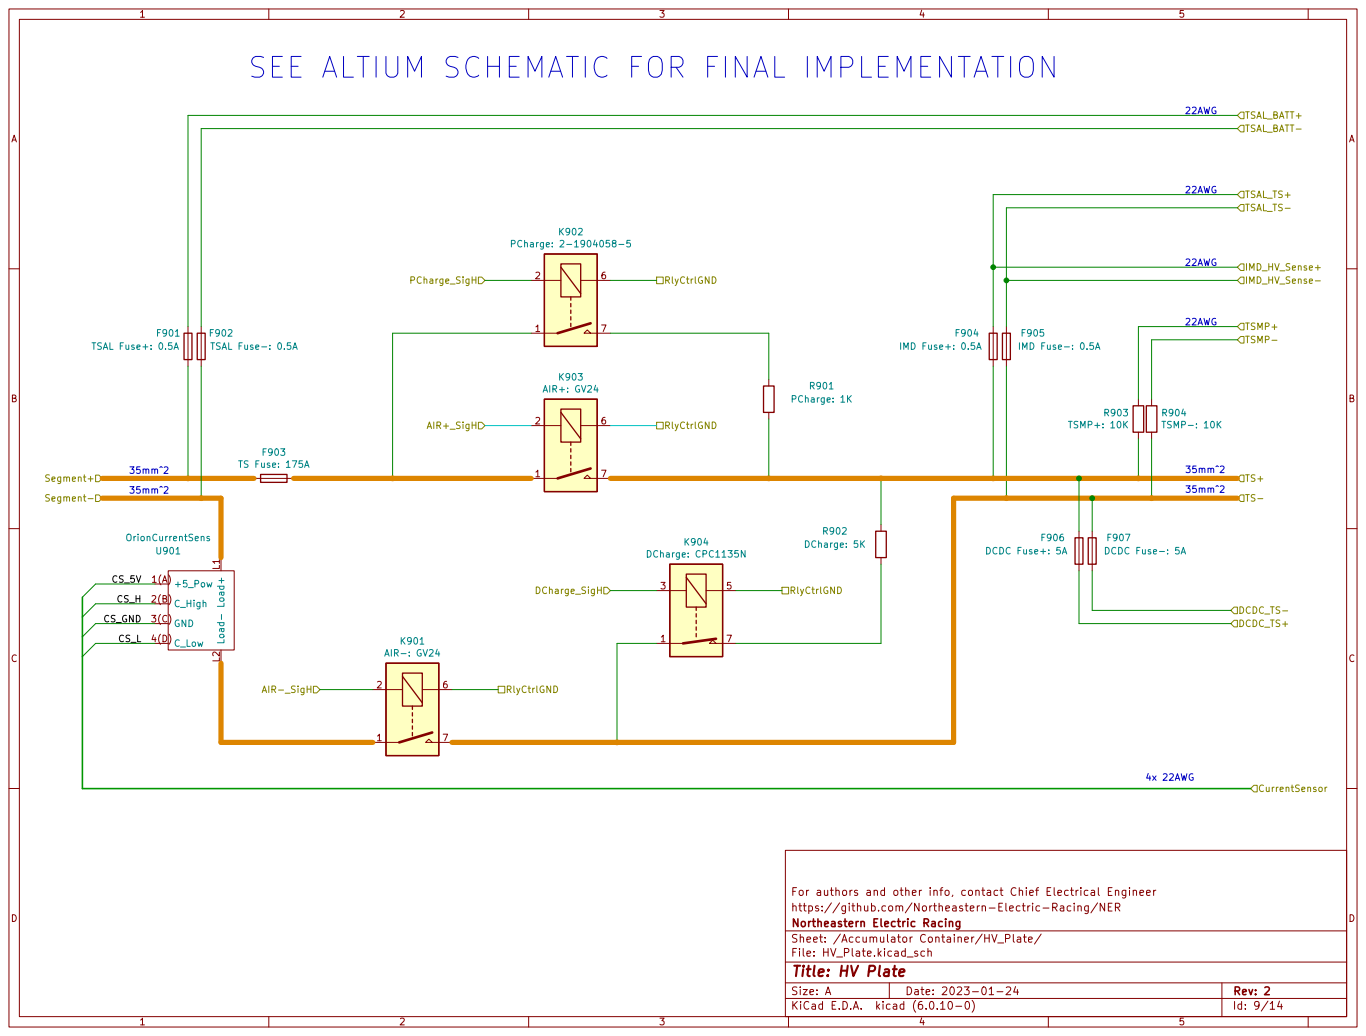
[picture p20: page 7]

22AWG SEE ALTIUM SCHEMATIC FOR FINAL IMPLEMENTATION

IMD_HV_Sense- TSMP+ TS+ TSMP- RlyCtrlGND

For authors and other info, contact Chief Electrical Engineer
https://github.com/Northeastern-Electric-Racing/NER
Northeastern Electric Racing
Sheet: /Accumulator Container/HV_Plate/
File: HV_Plate.kicad_sch
Id: 9/14 Title: HV Plate

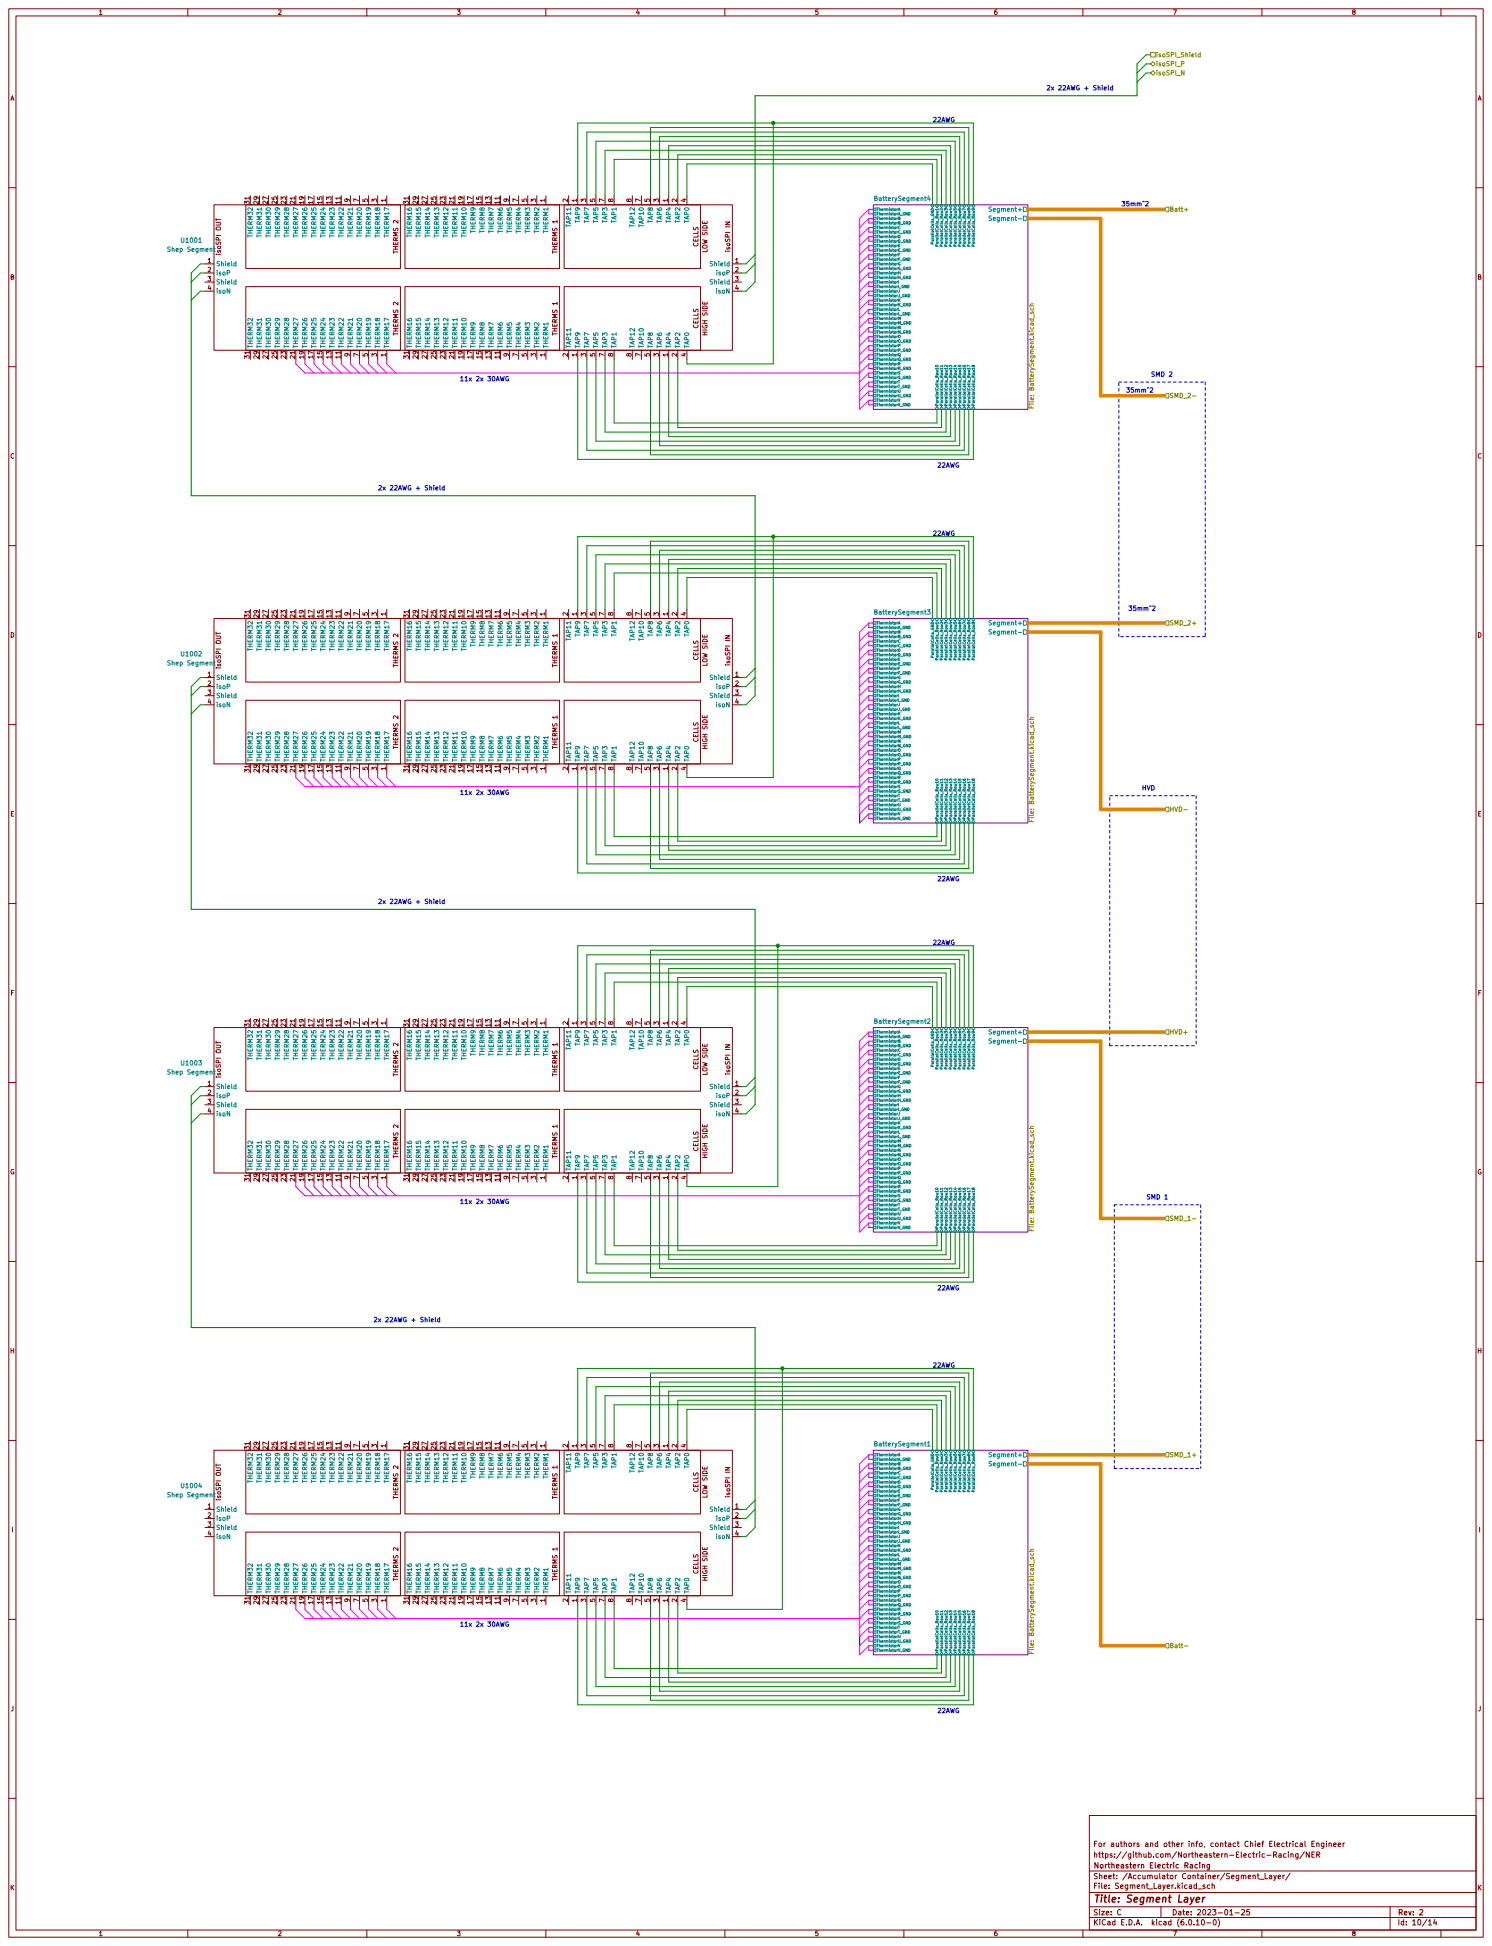
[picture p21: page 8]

For authors and other info, contact Chief Electrical Engineer
https://github.com/Northeastern-Electric-Racing/NER
Northeastern Electric Racing
Sheet: /Accumulator Container/Segment_Layer/
File: Segment_Layer.kicad_sch
Id: 10/14 Title: Segment Layer

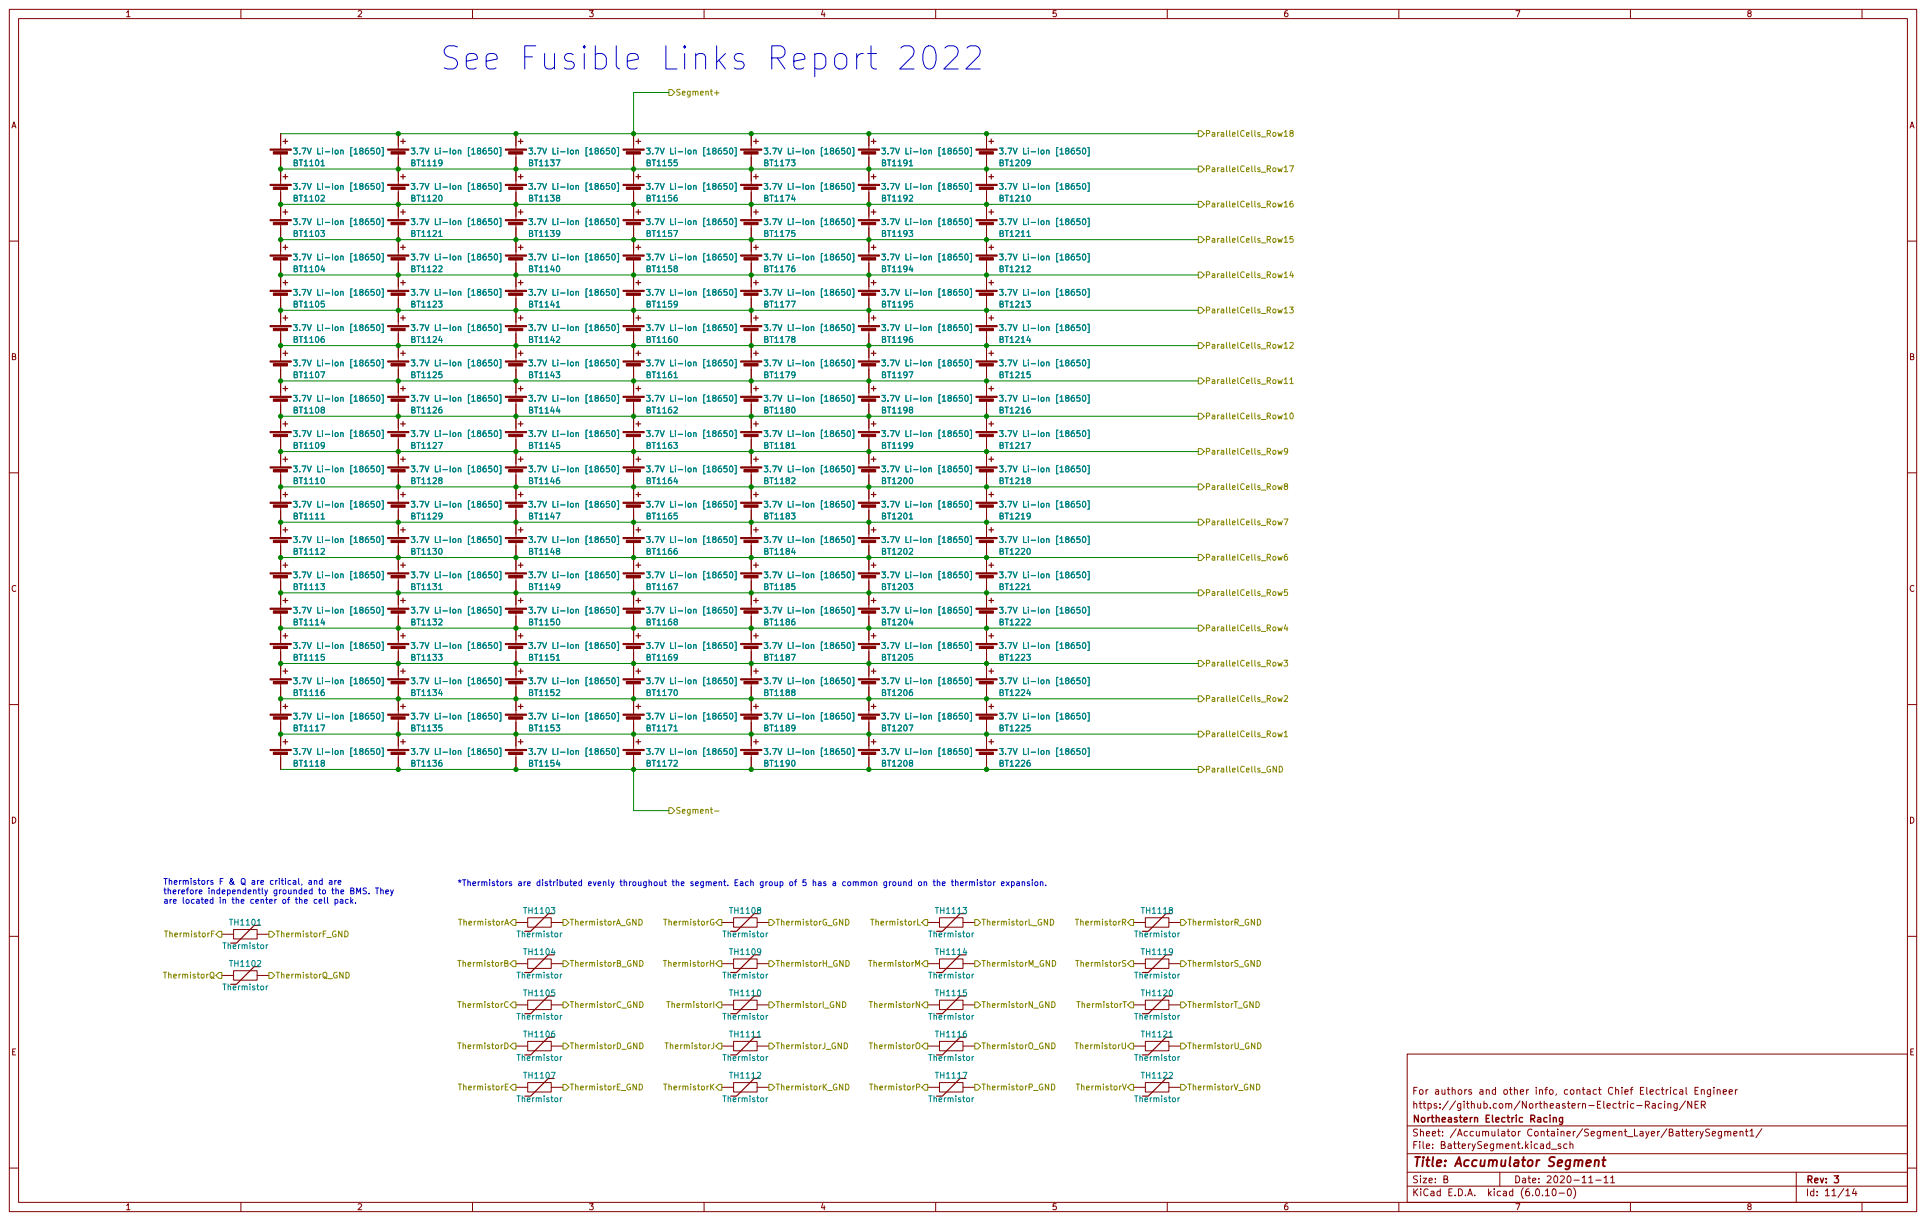
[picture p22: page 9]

See Fusible Links Report 2022
3.7V Li-Ion [18650] BT1108

Thermistors F & Q are critical, and are
therefore independently grounded to the BMS. They
are located in the center of the cell pack.

*Thermistors are distributed evenly throughout the segment. Each group of 5 has a common ground on the thermistor expansion.

For authors and other info, contact Chief Electrical Engineer TH1122 Thermistor TH1121 Thermistor

https://github.com/Northeastern-Electric-Racing/NER
Northeastern Electric Racing
Sheet: /Accumulator Container/Segment_Layer/BatterySegment1/
File: BatterySegment.kicad_sch
Id: 11/14 Title: Accumulator Segment

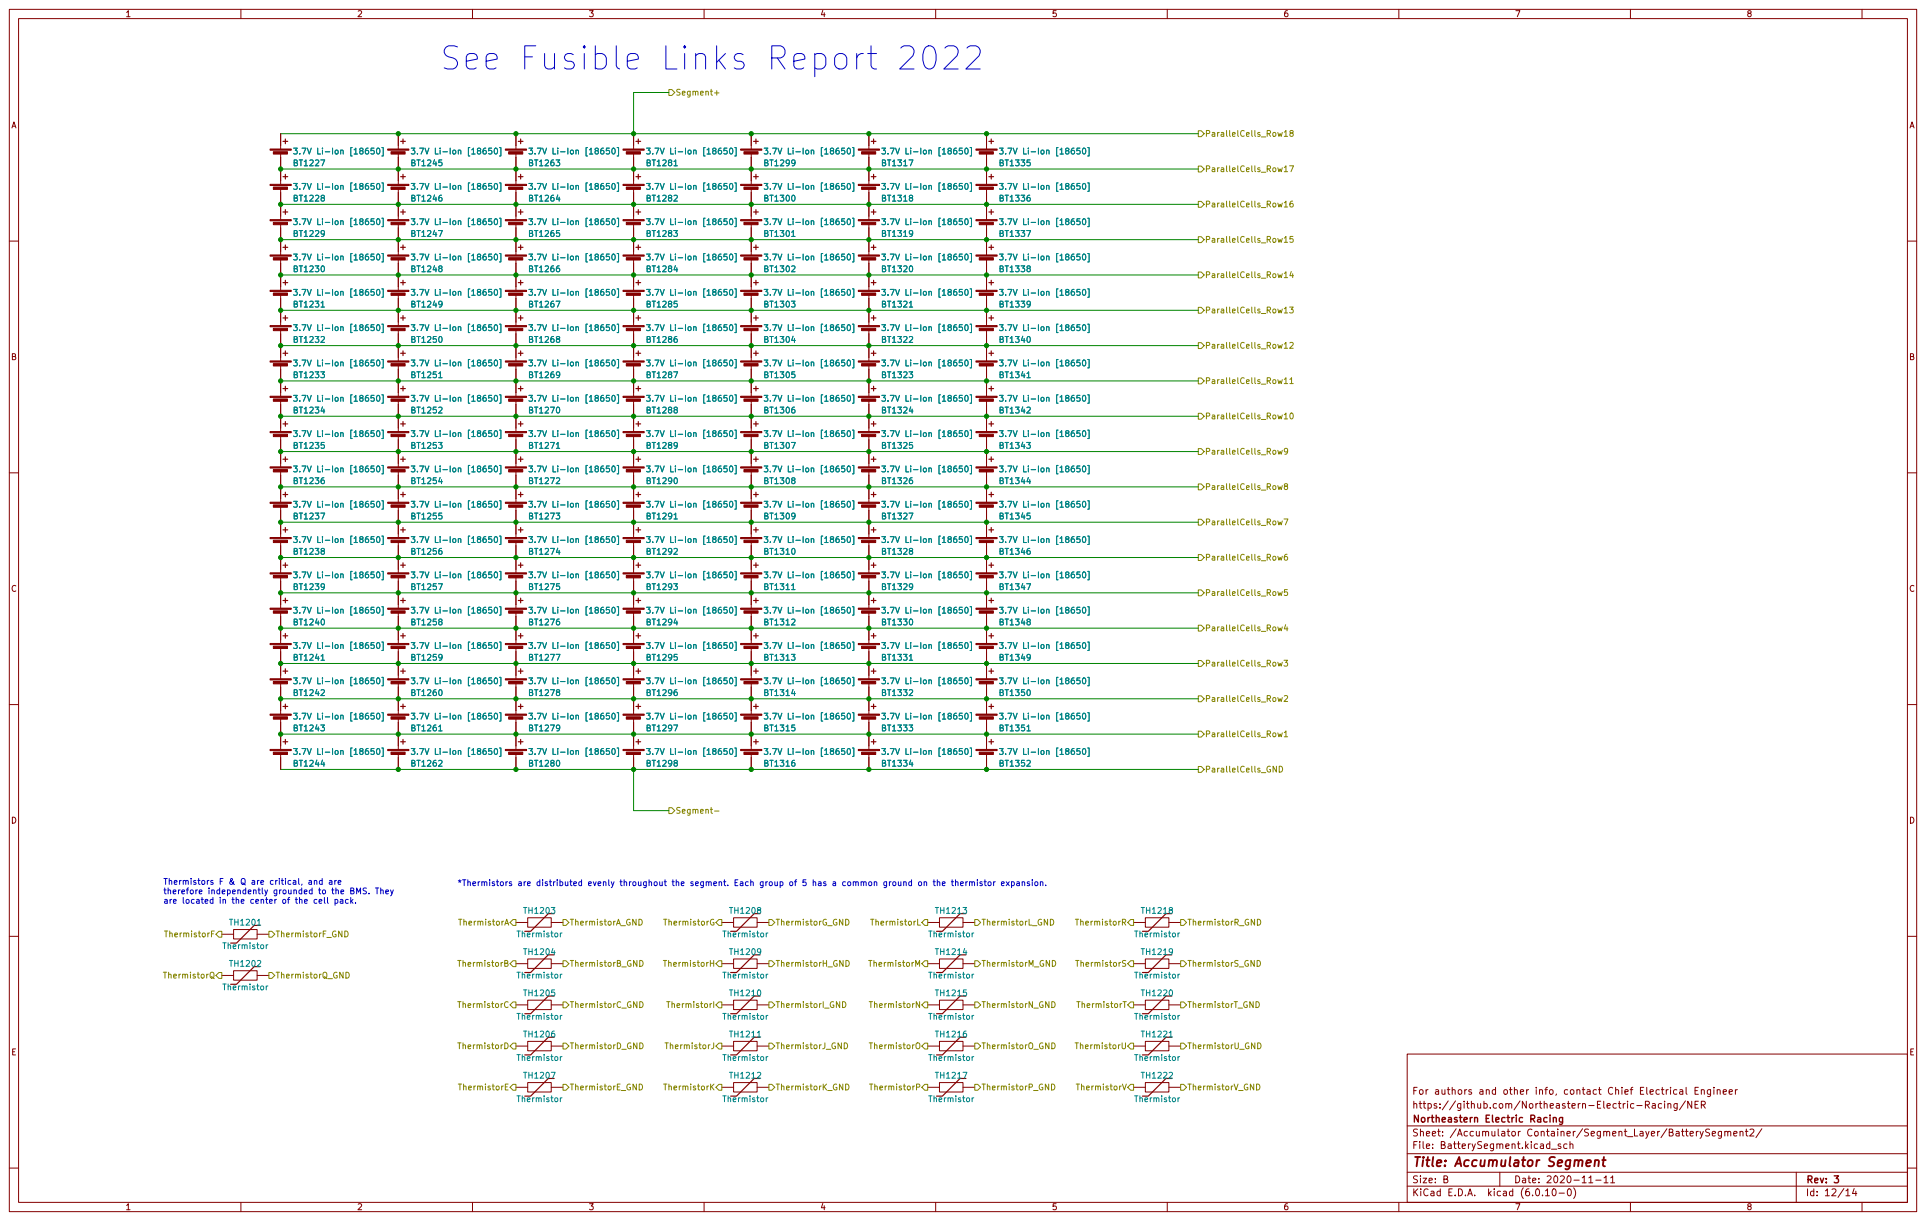
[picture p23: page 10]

See Fusible Links Report 2022
3.7V Li-Ion [18650] BT1233

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

For authors and other info, contact Chief Electrical Engineer TH1222 Thermistor TH1221 Thermistor
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

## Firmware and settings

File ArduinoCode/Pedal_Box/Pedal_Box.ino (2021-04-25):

#include <mcp_can.h>

// sensor pins
const int ACCEL_PIN1 = A0; 
const int ACCEL_PIN2 = A1; 
const int BRAKE_PIN1 = 2;
const int BRAKE_PIN2 = 3;

// brake switch and potentiometer values
int accelPin1Val; 
int accelPin2Val;
int brakePin1Val;
int brakePin2Val;

// state variables
bool invertorOn = false;
bool isForward = true;
bool brakePressed = false;
bool dischargeEnabled = false; // true when torque can be given to motor
bool chargeEnabled = false;    // true when regen torque is allowed
unsigned long timeBrake = 0;   // the time at which the brake was last pressed

// message timing values
const int COMMAND_MESSAGE_DELAY = 50; // in milliseconds
const int BRAKE_MESSAGE_DELAY = 50; // in milliseconds
const int BMS_MESSAGE_DELAY = 50;   // in milliseconds
unsigned long lastCommandMessage = 0; // the time the last command message was sent
unsigned long lastBrakeMessage = 0; // the time the last brake message was sent
unsigned long lastBMSMessage = 0; // the time the last BMS message was sent

// brake switch error variables
const int MAX_BRAKE_ERRORS = 5; // the maximum consecutive invalid brake switch readings before throwing an error
int currentBrakeErrors = 0; // current number of consectutive brake errors

// regen braking constants
const int START_TIME = 0;   // delay from when brake is pressed to when regen starts
const int MAX_TORQUE = 255; // maximum regen torque value
const int RAMP_TIME =  10;  // time until the maximum regen torque is reached (in seconds)
 
// CAN IDs  
const int CAN_START_MOTOR = 0x101;
const int CAN_DIRECTION = 0x102;
const int CAN_BRAKE = 0x103;
const int CAN_BRAKE_ERROR = 0x104;
const int CAN_ACCEL_ERROR = 0x105;
const int CAN_BMS_SHUTDOWN = 0x001;
const int CAN_MC_FAULTS = 0xAB;
const int CAN_BMS_STATES = 0x6B0;
const int CAN_BMS_FAULTS = 0x06;
const int CAN_MOTOR = 0xC0;

// CAN info
unsigned char len = 0; // length of incoming data
unsigned char buf[8];  // received data
unsigned long canId;   // CAN id of incoming message
const unsigned char MOTOR_OFF[8] = {0,0,0,0,0,0,0,0}; // message to turn motor off
const unsigned char ACCEL_ERROR[4] = {'P', 0, 5, 00}; // error message of "Vehicle Speed Sensor Malfunction" 
const unsigned char BRAKE_ERROR[4] = {'P', 0, 5, 04}; // error message of "Brake Switch A / B Correlation"
const unsigned char BMS_ERROR[8] = {0,1,0,0,0,0,0,0}; // error message for BMS to activate shutdown circuit

const int SPI_CS_PIN = 10; // base CAN pin

// function declarations
void readStates();
void readPotentiometers();
void readSwitches();

MCP_CAN CAN(SPI_CS_PIN); // setup can device

/**
 * Start CAN and initialize digital pins
 */
void setup() {
  Serial.begin(115200); // Initializes Serial communication

  while (CAN_OK != CAN.begin(CAN_250KBPS, MCP_8MHz)) { // specify 8MHz crystal
    Serial.println("CAN BUS init Failed"); // failure message
    delay(250); // delay, retry
  }
  Serial.println("CAN BUS Shield Init OK!"); // success message

  // Set brake light digital pins to act as inputs with built in pull-up resistors
  pinMode(BRAKE_PIN1, INPUT_PULLUP);
  pinMode(BRAKE_PIN2, INPUT_PULLUP);
}

/**
 * Continuoulsy read incoming CAN messages and the values of the accelerator potentiometers and brake switches
 */
void loop() {
  readStates();
  
  if ((millis() - lastCommandMessage) > COMMAND_MESSAGE_DELAY) { // Adds delay between pedal potentiometer readings
    if (invertorOn) { // only read potentiometers when the inverter is on
      readPotentiometers();
      lastCommandMessage = millis(); // reset command message time
    }
  }

  if ((millis() - lastBrakeMessage) > BRAKE_MESSAGE_DELAY) { // Adds delay between brake switch readings
    readSwitches();
    lastBrakeMessage = millis(); // reset brake message time
  }

  if((millis() - lastBMSMessage) > BMS_MESSAGE_DELAY) {  // Checks if BMS message is being recieved regularly 
    CAN.sendMsgBuf(CAN_BMS_SHUTDOWN, 0, 8, BMS_ERROR); // triggers shutdown circuit through BMS
  }
}

/*
 * readStates() reads the CAN messages from other parts of the car to set the following states:
 *  - CAN_START_MOTOR message is used to set the inverterOn state
 *  - CAN_DIRECTION message is used to set the isForward state
 *  - CAN_BMS_STATES message is used to set the dischargeEnabled and chargeEnabled states
 * and also reads fault messages from the motor controller in order to trigger the shutdown circuit via BMS
 */
void readStates() {
  if(CAN_MSGAVAIL == CAN.checkReceive()) {   // if a new message has been recieved.
    CAN.readMsgBuf(&len, buf);
    canId = CAN.getCanId(); // gets sender ID

    if (canId == CAN_START_MOTOR) {
      CAN.sendMsgBuf(CAN_MOTOR, 0, 8, MOTOR_OFF); // turns motor off to release lockout or because switch is off
      invertorOn = buf[0]; // set inverter state
    } else if (canId == CAN_DIRECTION) {
      isForward = buf[0]; // set direction state
    } else if (canId == CAN_BMS_STATES) {
      dischargeEnabled = buf[5] & 1;     // get first bit of Relay State byte
      chargeEnabled = (buf[5] >> 1) & 1; // get second bit of Relay State byte 
      lastBMSMessage = millis();
    } else if (canId == CAN_MC_FAULTS) {
      if ((buf[4] != 0) || ((buf[5] >> 3) & 1) || ((buf[5] >> 4) & 1)) { // only send message for fault bits 32-39, 43, 44
        CAN.sendMsgBuf(CAN_BMS_SHUTDOWN, 0, 8, BMS_ERROR); // triggers shutdown circuit through BMS
      }
    } else if (canId == CAN_BMS_FAULTS) {
      if (((buf[0] >> 5) & 1) || ((buf[0] >> 6) & 1)) { // only send message for cell voltage too high/low faults
        CAN.sendMsgBuf(CAN_BMS_SHUTDOWN, 0, 8, BMS_ERROR); // triggers shutdown circuit through BMS
      }
    }
  }
}

/**
 * Read the values of the two accelerator pedal potentiometers
 * Compare them to make sure the values agree and send value to CAN
 */
void readPotentiometers() {
  accelPin1Val = analogRead(ACCEL_PIN1); 
  accelPin2Val = analogRead(ACCEL_PIN2);

  if(accelPin1Val == 0 || accelPin2Val == 0 || accelPin1Val == 1023 || accelPin2Val == 1023){
    CAN.sendMsgBuf(CAN_BMS_SHUTDOWN, 0, 8, BMS_ERROR);
    CAN.sendMsgBuf(CAN_MOTOR, 0, 8, MOTOR_OFF);
    CAN.sendMsgBuf(CAN_ACCEL_ERROR, 0, 4, ACCEL_ERROR);
  }

  if (abs(accelPin1Val - accelPin2Val) <= (1023 * 0.1)) {
    unsigned char accelTorque = 0;
    unsigned char regenTorque = 0;

    if (dischargeEnabled) {  // acceleration torque is allowed
      int averageReading = (accelPin1Val + accelPin2Val) / 2;
      accelTorque = averageReading / 4;
    } 
    
    if (chargeEnabled && brakePressed) {  // regen torque is allowed 
      int timeDifference = (millis() - timeBrake) / 1000; // length of time the brake has been pressed
      if (timeDifference - START_TIME > RAMP_TIME) { // max regen torque is allowed
        regenTorque = MAX_TORQUE;
      } else if (timeDifference - START_TIME > 0) {
        regenTorque = timeDifference * (MAX_TORQUE / RAMP_TIME); // regen torque depends on how long the brake has been held
      }
    }
    
    unsigned char message[8] = {accelTorque,regenTorque,0,0,isForward,1,0,0};
    CAN.sendMsgBuf(CAN_MOTOR, 0, 8, message); // send message to motor controller with torques and direction
  } else {  // send shutdown message, turn off motor, and send error message
    CAN.sendMsgBuf(CAN_BMS_SHUTDOWN, 0, 8, BMS_ERROR);
    CAN.sendMsgBuf(CAN_MOTOR, 0, 8, MOTOR_OFF);
    CAN.sendMsgBuf(CAN_ACCEL_ERROR, 0, 4, ACCEL_ERROR);
  }
}

/**
 * Read the values of the two brake switches
 * Compare them to make sure the values agree and send value to CAN
 */
void readSwitches() {
  brakePin1Val = digitalRead(BRAKE_PIN1);
  brakePin2Val = digitalRead(BRAKE_PIN2);

  if ((brakePin1Val == LOW) && (brakePin2Val == LOW)) {  // both switches are on
    if (!brakePressed) {  // set the brake time if the brake has just been pressed
      timeBrake = millis();
    } 
    brakePressed = true;
    currentBrakeErrors = 0;
    CAN.sendMsgBuf(CAN_BRAKE, 0, 1, {1});
  } else if ((brakePin1Val == HIGH) && (brakePin2Val == HIGH)) { // both switches are off
    brakePressed = false;
    currentBrakeErrors = 0;
    CAN.sendMsgBuf(CAN_BRAKE, 0, 1, {0});
  } else {  // error due to switches having different values
    brakePressed = false;
    currentBrakeErrors++;
    if (currentBrakeErrors >= MAX_BRAKE_ERRORS) { // send shutdown message, turn off motor, and send error message
      CAN.sendMsgBuf(CAN_BMS_SHUTDOWN, 0, 8, BMS_ERROR);
      CAN.sendMsgBuf(CAN_MOTOR, 0, 8, MOTOR_OFF);
      CAN.sendMsgBuf(CAN_BRAKE_ERROR, 0, 4, BRAKE_ERROR);
    }
    
  }
}

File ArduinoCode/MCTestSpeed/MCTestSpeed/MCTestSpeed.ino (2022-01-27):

/*
   Author: Joshua Cheng
   Date: March 11, 2021

   Pinouts:
   MOSI - pin 11
   MISO - pin 12
   CLK - pin 13
   SS - pin 10

*/
#include <mcp_can.h> // Uses Seeed-studio's CAN_BUS_Shield library.

#define CAN_SS_PIN 10
#define HARD_SPEED_LIMIT 6500
#define CAN_MOTOR 0xC0 // canID for msg to send to motor controller
const unsigned char MOTOR_OFF[8] = {0, 0, 0, 0, 0, 0, 0, 0}; // message to turn motor off

MCP_CAN CAN(CAN_SS_PIN);

bool isForward = true;
bool isOn = false;
unsigned int speedLow = 0;
unsigned int speedHigh = 0;
unsigned long lastCommand = 0;

/**
   Sets relavent pins to output or input, initializes serial for debugging, initializes CAN module
*/
void setup() {
  Serial.begin(9600);

  while (CAN_OK != CAN.begin(CAN_500KBPS, MCP_8MHz)) { //specify 8MHz crystal
    Serial.println(F("CAN BUS init Failed"));
    delay(250);
  }
  Serial.println(F("CAN BUS Shield Init OK!"));
  Serial.println(F("Please set your serial monitor to 'Both NL & CR' near the bottom. "));
  Serial.println(F("Type a numerical value to set the speed or"));
  Serial.println(F("'reverse' to change the direction or 'on'/'off' to turn the MC on or off."));
}

/**
   Prints incoming CAN messages to the Serial Monitor, allows user to send CAN messages via the Serial Monitor.
*/
void loop() {
  String serialIn = "";
  while (Serial.available() > 0) {
    serialIn = Serial.readStringUntil('\r');
  }

  // handle user input
  if (serialIn.length() > 0) {
    if (serialIn.equals("reverse")) {
      isForward = !isForward;
      Serial.print(F("Reversing... Direction is now: "));
      if (isForward) {
        Serial.println(F("forward"));
      } else{
        Serial.println(F("backwards"));
      }
    } else if (serialIn.equals("on")) {
      Serial.println(F("Turning on motor controller"));
      CAN.sendMsgBuf(CAN_MOTOR, 0, 8, MOTOR_OFF); // release lockout
      speedLow = 0;
      speedHigh = 0;
      isOn = true;
      isForward = true;
    } else if (serialIn.equals("off") && isOn) {
      Serial.println(F("Turning off motor controller"));
      CAN.sendMsgBuf(CAN_MOTOR, 0, 8, MOTOR_OFF);
      isOn = false;
    } else if (serialIn.equals("0") || (serialIn.toInt() > 0 && serialIn.toInt() <= HARD_SPEED_LIMIT)) {
      Serial.println("Setting speed value: " + serialIn);
      speedLow = serialIn.toInt() % 256;
      speedHigh = serialIn.toInt() / 256;
    }
  }

  // send command message if MC is on and its been 50ms
  if ((millis() - lastCommand) > 50) {
    lastCommand = millis();
    unsigned char message[8] = {0,0,speedLow,speedHigh,isForward,isOn,0,0};
    CAN.sendMsgBuf(CAN_MOTOR, 0, 8, message);
  }
  
  // send command message if MC is of and its been 50ms
  if (!isOn && (millis() - lastCommand) > 50) {
    lastCommand = millis();
    CAN.sendMsgBuf(CAN_MOTOR, 0, 8, MOTOR_OFF);
  }

  

  if (CAN_MSGAVAIL == CAN.checkReceive()) { //if a new message has been recieved.
    unsigned char len = 0; // Length of incoming message
    unsigned char buf[8]; // Memory for incoming message
    int canId; // Sender's ID
    CAN.readMsgBuf(&len, buf); //enters message into program
    canId = CAN.getCanId(); //gets sender ID

    Serial.print(F("Message Recieved from CAN ID: "));
    Serial.print(String(canId));
    Serial.print(F("  |  message: "));
    for (int i = 0; i < 8; i ++) {
      Serial.print(String(buf[i]));
      Serial.print(F(" | "));
    }
    Serial.println();
  }
}

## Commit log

2020-11-01 Fixed Relay Connections
    Moved connection from signal pin to open pwm arduino pin, sent + pin connection to 5V arduino pin.
    [Brake Light.sch, Driver IO Enclosure.sch]
2020-11-01 Added CAN_SHIELD to Driver IO
    Added CAN_SHIELD to Driver IO and grounded the CAN_SHIELD to the chassis for the dashboard can box and grounded the CAN_SHIELD to the arduino ground in the brake light can box
    [Brake Light.sch, Master System Schematic.sch]
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2020-11-01 Fixed Title Block and Sheet Size
    [Brake Light.sch, Driver IO Enclosure.sch, TSAL_Circuit.sch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]
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2020-11-03 Rotated first section of GLV
    Increased sheet size (May still downsize back to C)
    Moved GLV from CHS GND to fusebox
    [Master System Schematic.sch]
2020-11-03 Created Fan Banks and Moved Latching
    Created the accumulator cooling fan banks in schematic
    Began moving the latching circuits
    [Master System Schematic.sch]
2020-11-03 Reducing schematic to blocks
    Stripped down everything to just the heirarchical sheets and their respective master sheet components
    [Master System Schematic.sch, Shutdown_LatchingCircuits.sch]
2020-11-03 Laid out blocks tentatively
    Generally placed heirarchical sheets. Will be moved as wires are placed
    [Master System Schematic.sch]
2020-11-03 Cleaned up CAN boxes
    Includes Brake Light, Pedalbox, Driver IO
    Fixed spacings, sizing, layout, etc
    [Master System Schematic.sch]
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2020-11-03 IMD Container
    Added IMD into a container
    Wired the IMD
    + Some extra bits
    [Accumulator_Container.sch, BMSContainer.sch, BatterySegment.sch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]
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2020-11-03 Relocated MC into the BMS Container
    Representing merging of MC into BMS container
    Starting some wiring
    [Accumulator_Container.sch, BMSContainer.sch, Brake Light.sch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]
2020-11-03 Corrected MC control relays
    Connected to one ground
    Added pin to heirarchical sheet for main contactor (but needs new MC model
    Also added assorted grounds
    [Accumulator_Container.sch, BMSContainer.sch, Master System Schematic.sch]
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2020-11-03 Misc
    Connected IMD fault line
    Replaced charger CAN wires with a bus and shielding
    Connected TSMPs
    [BMSContainer.sch, IMD_Container.sch, Master System Schematic.sch]
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2020-11-09 Revert "Update Pedal_Potentiometers.ino"
    This reverts commit 6c86daaa20c00895562dd0201d3ed7a06a294e7c.
    [Pedal_Potentiometers.ino]
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2020-11-11 Wiring Cleanup and sheet pin fixing
    [BMS-MC_Container.sch, BatterySegment.sch, Master System Schematic.sch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]
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2020-11-12 fixed therm boards
    fixed therm board implementation
    beginning accumulator redraw
    [Accumulator_Container.sch, BMS_Container.sch, BatterySegment.sch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]
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2020-11-13 Fixes to Matt's comments
    > Title block comments moved to top two lines
    > Paper size set to A and schematic adjusted
    > Deleted PCB file
    > Fixed minor things I noticed
    Version 1.1
    [BMSBoard.kicad_pcb, BMSBoard.sch]
2020-11-13 Added to Title Block
    Added company name, Github link, and general attribution info
    [BMSBoard.sch]
2020-11-13 Quick fix
    > Noticed and deleted BMSIn12V line, would be the same as PWR_Ready
    [BMSBoard.sch]
2020-11-14 BMS Control Board V2
    > Fan relay removed, BMS will be passively cooled.
    > Ground sourced from chassis through quick connect spade connector.
    > Diode from Charger Power to GLV replaced with a relay.
    > Connectors added for all control board IO.
    > Fusing to be added later today.
    Version 2
    [BMSBoard.sch]
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2020-11-15 Fusing
    > Added fuses for pump, pwr_charge, pwr_ready, and thermistor expansion.
    > Minor fixes
    Version 2.1
    [BMSBoard.sch]
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2020-11-15 fixed motor lines
    [Master System Schematic.sch]
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2020-11-15 Charging Schematic Updates
    Added Shielding, added fuses, rearanged F1, removed 2 pin connector.
    [Charger.sch, Master System Schematic.sch, ThermistorPCB.sch]
2020-11-16 Fixed mistakes
    Deleted unneeded shielding line and neutral fuse line
    [Charger.sch, Master System Schematic.sch]
2020-11-16 Moved F86 to Positive line
    Another quick fix moving F86 to Positive line from neutral
    [Charger.sch]
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2020-11-19 Minor Fixes
    > Fixed some minor issues
    [BMSBoard.sch]
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2020-11-23 Minor fuse change
    > Moved F2 to the other side of the relay.
    Version 2.3
    [BMSBoard.sch]
2020-11-24 removed bms fan
    no longer needed
    [Master System Schematic.sch]
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2020-11-24 Connected CAN
    CAN bus was connected to wrong pins on the MC
    [Master System Schematic.sch, Shutdown_LatchingCircuits.sch, TSAL_Circuit.sch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]
2020-11-24 Fixed paper choice for VT board
    [VT_PCB.sch]
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2020-12-03 Stylistic changes and size consolidation
    > Combined GLV_PWR and Charge_PWR into the 3 pin connector GLV/Charge_PWR
    > Replaced K4 with a schottky diode (D1)
    > Major sytlistic changes, replaced net labels with wires
    Version 3.0
    [BMSBoard.sch]
2020-12-04 Minor fixes and pin changes
    > Fixed connection to K1
    > Changed pin order on BMS_Signal, Therm_Signal, GLV/Charge_PWR, BMS_PWR
    Version 3.1
    [BMSBoard.sch]
2020-12-05 MOSFET Switching
    > Replaced relays with mosfets
    > Added control logic for mosfets
    > Added ideal diode controller for charge power lockout
    Version 4
    [BMSBoard.sch]
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2020-12-13 Added Wire Shielding
    CAN_Shielding was added along with a 6 Pin connector to reflect our chage to a 6 pin connector. Also TS Shielding was indicated inside the box that it was being grounded to earth.
    [Charger.sch, Master System Schematic.sch]
2020-12-13 Really small wiring change
    just barely moved a wire junction for aesthetics
    [BMS_Container.sch, Charger.sch, Master System Schematic.sch]
2020-12-15 Added motor resolver interface
    [Master System Schematic.sch]
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2021-01-17 Missing annotation
    Annotated MC resistor
    [Brake Light.sch, Driver IO Enclosure.sch, Master System Schematic.sch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]
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2021-01-17 Replaced bus with wire
    Someone randomly used some bus in the middle of a wire run?? I did a fixie
    [IMD_Container.sch, Master System Schematic.sch, Shutdown_LatchingCircuits.sch]
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2021-01-19 Added/Fixed Sheet Connections Within BMS Container
    > Added hierarchical labels for each input on the VPM and connected them to hierarchical labels and the BMS within the BMS container.
    > Added CANS(Charger) hierarchical label coming out of the BMS container sheet and connected it to the charger CAN bus line.
    BMS Container Version 8.1
    [Accumulator_Container.sch, BMS_Container.sch, BatterySegment.sch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]
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2021-01-19 Added delay for CAN messages
    Added a delay when sending the brake and pedal command messages to avoid overloading the CAN network. Delay is currently 50 ms.
    [Pedal_Box.ino]
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2021-01-24 Little tiny bitty fix
    Removed Discharge limit connection
    Moved motor a wee
    [BMS_Container.sch, Master System Schematic.sch]
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2021-01-31 Removed MC on/off backups
    Realized that the discharge_en and charge_en pins are not strictly necessary, and implementation is not as straightforward as originally thought. All current limiting will be done via can, and we hav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
    [BMS_Container.sch, Master System Schematic.sch]
2021-01-31 Reversed Polarity of Shutdown latch
    The BMS MP_en which drives the shutdown latch is active low (ON) when there are NO faults present. When a critical DTC is present, or when a certain CANBUS message is recieved from the pedal box, the output will turn OFF (floats high), latching the relay open. If the output returns to normal (ON, active low), the relay will energize and close the shutdown loop
    [Shutdown_LatchingCircuits.sch]
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2021-02-01 Added Shutdown circuit indicator resistors and BMS connectors
    Realized that the 470 ohm resistors were missing from shutdown latching circuit
    started adding bms connectors
    [BatterySegment.sch, Master System Schematic.sch, Shutdown_LatchingCircuits.sch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]
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2021-02-01 Added NEW esf2 shutdown summary, replaced old one
    only changes were voltage tap relays
    [IMD_Container.sch, ShutdownSummary.sch, Shutdown_Summary.sch]
2021-02-08 Added bms connectors, ensured all up to date
    made final bms project edits to ensure accuracy of schematic
    [Accumulator_Container.sch, BMS_Container.sch, Master System Schematic.sch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]
2021-02-10 Update Pedal_Box.ino
    Checks for open and short circuit for potentiometer
    [Pedal_Box.ino]
2021-02-12 VPM Board Flyback Diode
    > Added MBRD5100 diode for protection against voltage spikes when switching the motor.
    > Added note explaining this ^
    VPM Board Version 4.3
    [Master System Schematic.sch, VPMBoard.sch]
2021-02-12 Revert "Merge branch 'Dylan_BMS-control-systems-slight-rework' of https://github.com/Northeastern-Electric-Racing/NER into Dylan_BMS-control-systems-slight-rework"
    This reverts commit fde7ba4e4a38cad13224d6abfd117b52e4ba179f, reversing
    changes made to 479d55be7c023c6502d2d4db07d9957a4b0a3a94.
    [Accumulator_Container.sch, BMS_Container.sch, Master System Schematic.sch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]
2021-02-12 Revert "Revert "Merge branch 'Dylan_BMS-control-systems-slight-rework' of https://github.com/Northeastern-Electric-Racing/NER into Dylan_BMS-control-systems-slight-rework""
    This reverts commit 7bfceb9de4e286d5e46c7b991145f3115c617458.
    [Accumulator_Container.sch, BMS_Container.sch, Master System Schematic.sch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]
2021-02-12 Revert "VPM Board Flyback Diode"
    This reverts commit 479d55be7c023c6502d2d4db07d9957a4b0a3a94.
    [Master System Schematic.sch, VPMBoard.sch]
2021-02-12 VPM Board Update
    > Reset back to dylan's last commit
    > Added flyback diode for protection of pump switching circuit
    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
    [BMS_Container.sch, Master System Schematic.sch, VPMBoard.sch]
2021-02-15 Add kickback of BMS faults
    Pedal box receives the BMS DTC broadcast message and sends the BMS shutdown CAN message if the cell voltage too high/low faults are active.
    [Pedal_Box.ino]
2021-02-15 Update brake switch behavior
    Add a counter for the number of times the two brake switches disagree with each other before entering an error state.
    [Pedal_Box.ino]
2021-04-07 Master Schematic and VPM Changes
    > Thermal Expansion and Critical Therm busses combined into Temperature_Data in Accumulator_Container.sch
    > BattFanPWM added to Temperature_Data connector
    > PumpIO connector changed from 2 to 4 pins
    > Added 7-Pin Generic connector
    > Updated VPM board schematic
    VPM Version 5
    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
    [Accumulator_Container.sch, BMS_Container.sch, Brake Light.sch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]
2021-04-16 HV Plate
    > Added HV_Plate, LV_Plate, and Segment_Layer subsheets to batbox
    > Recreated current HV circuit in HV_Plate sheet
    > Added placeholders for HV_Plate wire sizes
    > Added outputs in HV_Plate sheet
    > Added component datasheets for HV circuit
    HV_Plate V1.0
    [Accumulator_Container.sch, BMS_Container.sch, BatterySegment.sch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]
2021-04-16 Segment Layer
    > Added segments to Segment_Layer sheet
    > Added VT PCBs and Thermistor PCBs to Segment_Layer sheet
    > Removed relays from VT PCBs
    > Still need to add connectors to VT and Thermistor PCBs once PCBs have been redesigned
    > Added outputs for Segment_Layer sheet
    > Added wire gauges to Segment_Layer sheet
    Segment_Layer V1.0
    [Accumulator_Container.sch, BMS_Container.sch, BatterySegment.sch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]
2021-04-19 LV Plate
    > Added basic connectors and outlines for MCR PCB
    > Added and wired components on LV Plate
    > Added GLV connector
    > Connected layers
    > Some wire gauges still needed
    LV_Plate Version 1.0
    [Accumulator_Container.sch, BMS_Container.sch, BatterySegment.sch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]
2021-04-21 LV Plate Cleanup + Other Small Stuff
    > Renamed MCR PCB to BattBox PCB
    > Added 7 Pin IMD connector to BattBox PCB
    > Fixed wire gauges on Segment Layer sheet
    > Added HV cutout on LV Plate
    > Added fan signals
    > Deleted old accumulator stuff
    > Added BattBox and BMS fans
    BattBox PCB V1.0
    [Accumulator_Container.sch, BMS_Container.sch, BattBoxPCB.sch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]
2021-04-21 Master Cleanup
    > BattBox sheet tweaks
    > Removed IMD container
    > Removed BattBox fans from master
    > Removed BMS container, temporarily moved VPM sheet
    [Accumulator_Container.sch, BattBoxPCB.sch, BatterySegment.sch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]
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2021-10-19 ESF 1 2021-22 updates (#101)
    -Added CAN shutdown switch
    -Removed isolation relays for volt taps
    -Fixed error with discharge wiring
    -Cleaned
    [IMD_Container.sch, Shutdown_Summary.sch]
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2021-12-03 Battery Box KiCAD Update (#103)
    * LV Plate and VPM board
    Verified and updated LV plate connections
    Setup VPM board stand-in
    Organized main battery box schematic
    * Battbox and master update
    - Fixed all connections within battbox and did some formatting
    - Added all battbox connections to master
    * Annotations complete
    * VPM callout
    Added call to view altium schematic for VPM boarrd
    * TSAL call out
    Redirect to altium for TSAL
    * Dates and stuff
    - Final annotations
    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
    [Accumulator_Container.sch, BattBoxPCB.sch, BatterySegment.sch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]
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2021-12-19 Pin swap (#105)
    [Accumulator_Container.sch]
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2022-01-27 Fixes (#107)
    -Sense line 3 fixed
    -Recalibrated voltage offset
    [CellVoltageMeasurement.ino]
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2022-01-29 Created new sheet for footwell
    Created new sheet and added an arduino
    [Accumulator_Container.sch, BattBoxPCB.sch, BatterySegment.sch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]
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2022-02-02 Revert "Footwell box updates" (#112)
    [Accumulator_Container.kicad_sch, Accumulator_Container.sch, BattBoxPCB.kicad_sch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]
2022-02-02 Matt updates (#109)
    * Clean up and update
    - Updated some schematics to KiCAD 6
    - Updated NER library to KiCAD 6
    - Minor cleaning to some accumulator pages
    * Clean up
    - Cleaned TSAL
    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
    [Accumulator_Container.kicad_sch, BattBoxPCB.kicad_sch, BatterySegment.kicad_sch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]
2022-02-03 Footwell integration fix (#113)
    * Beginning footwell fix
    adding in
    * Finished box, doing celeanup
    * Cleaning up can wires
    * Added non critical power
    * Added misc indicators
    * replaced old chassis markers
    * fixing pin input/output/passive status
    * Consolidation (part 1)
    * Consolidation (part 2)
    * Consolidation part 3 complete
    #Scope creep
    * weird autosave issue
    * Fixing pin directions and grounds
    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
    [Accumulator_Container.kicad_sch, BatterySegment.kicad_sch, Brake Light.kicad_sch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]
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2022-02-03 Dylan cleanup and continualupdates (#114)
    * Annotations
    * Added custom Chassis GND symbol
    [Accumulator_Container.kicad_sch, BatterySegment.kicad_sch, Brake Light.kicad_sch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]
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2022-02-05 Added missing 12V in latching
    Missing 12V to CAN fault pole
    [Accumulator_Container.kicad_sch, Brake Light.kicad_sch, Charger.kicad_sch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]
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2022-02-08 Updates after motor tests
    Updates after running and testing the code with the BMS and the MC connected via CAN. Fixed many logical issues
    [MotorControllerTest.ino, main.cpp]
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2022-02-09 Peter telemetry dev (#119)
    * Test with MC and BMS
    * updates
    * Updates after motor tests
    * Initial EEPROM code
    Add initial code for using EEPROM to store program constants to allow for updates over CAN.
    * Add flow rate test project
    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
    [EEPROM_SD_SENSOR_test_CAN.ino, EEPROM_SD_SENSOR_test_basic.ino, EEPROM_test_basic.ino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]
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2022-03-24 Flipped negative + fixed units
    [main.cpp]
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2022-04-05 Peter telemetry dev (#126)
    * TCU updates for testing
    * Processing scripts for drive test
    * Add logs and outputs files
    * OOp
    * More panic code
    * oop
    * Adding fault reset
    * fixy
    * TelemetryData-4/2/22
    Telemetry data collected by NERduino over initial 4/2/22 outdoor testing.
    * Add Multiple Buffers and RTC Support
    [testOutputs.csv, testing-4-2-22.csv]
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2022-04-12 Fix import file path issues
    [fileDataDisplay.py, sendToInflux.py]
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2022-07-31 Save progress (May have errors)
    [fileDataDisplay.py, main.cpp, xbeeDataHandler.py]
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2022-08-10 Matt final comp updates (#130)
    * Master schematic fixes
    - readded charge backpower
    - Added Driver io LV batt guage
    - Thickened wires
    - swapped 2awg to 35mm2
    * Exporting
    * TS main fuse
    Changed from 200 to 175
    * Fixed sheet size
    * Updated charger wire guage
    thicc
    * Fixed footwell sheet
    [Accumulator_Container.kicad_sch, BattBoxPCB.kicad_sch, Brake Light.kicad_sch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]
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2022-09-22 Matt matlab code 2 (#133)
    * V2 script + git ignore
    New script that works with the new format of the telemetry hub CSV output while we wait for hub graphing improvements
    - also added .csv to git ignore
    * V3 code
    Uses the synchronize function to allow us to set exactly how many samples we want from the data. Runs much faster, although there are more optimizations that could be made if needed
    * Updated for peters new IDs
    * Fixed polarity
    Telem hub now does the reversals, so we dont need to
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2023-02-23 ESF-2 2023 Updates (#136)
    * Moved shutdown loop & TSMPs
    * Moved Dashboard/Footwellbox
    * Deleted SSOKs
    * More stuff
    * Charger and battbox stuff
    * Added battbox fans
    * Updated sheet sizing
    * Flipped MC
    to make powertrain ordering better
    * Updated HV plate
    * IDrk
    * Better topsheet labels
    * Segment Layer updates
    Adding shepherd
    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
    [Accumulator_Container.kicad_sch, Accumulator_Container.sch, BMS_Container.sch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]
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2023-03-26 James precharge calcs 2023 (#138)
    * Moved 17 to folder
    * Put in precharge current calculator
